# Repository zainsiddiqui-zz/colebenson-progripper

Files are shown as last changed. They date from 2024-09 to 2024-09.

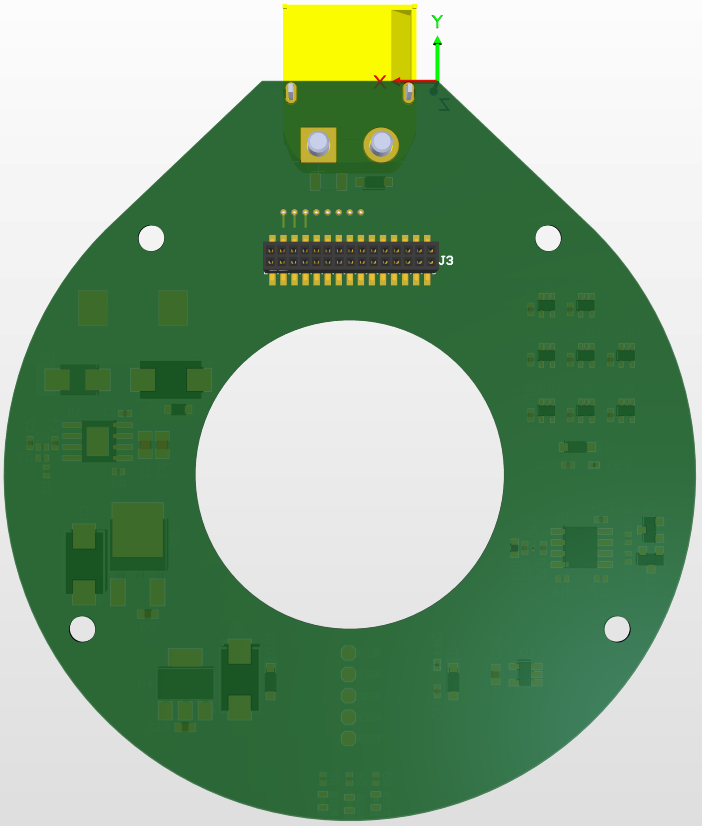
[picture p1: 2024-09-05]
Design Files/LSS_Gripper_Top_Board/Renderings/TopBoard-Bottomside.png

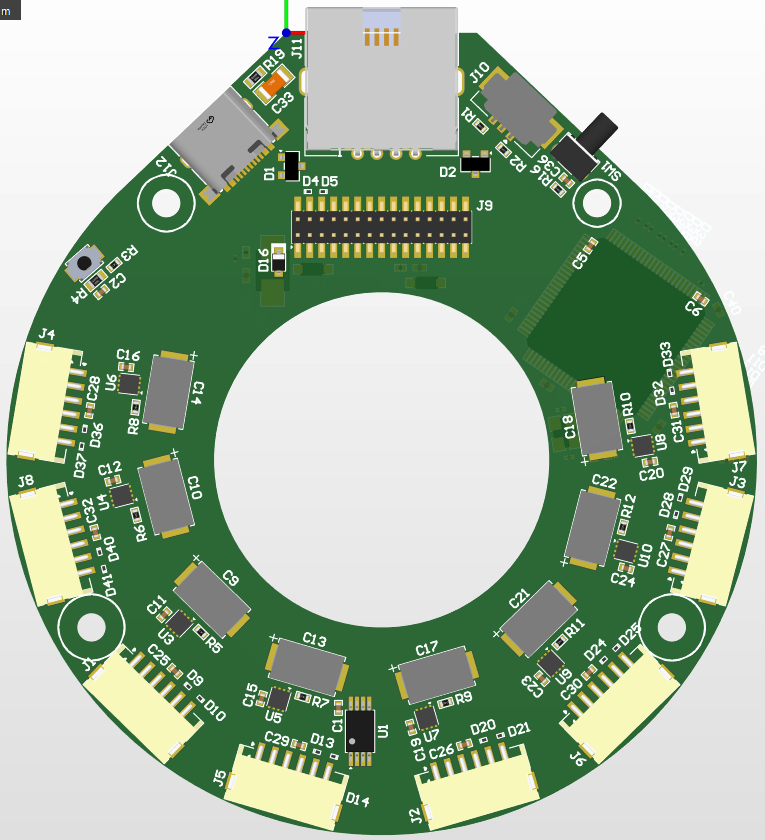
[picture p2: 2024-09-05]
Design Files/LSS_Gripper_Bottom_Board/Renderings/BottomBoard-Topside.png

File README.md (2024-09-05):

# LSS Modular Variable Gripper
### Client Name: Cole Benson (Robotshop)

## Requirements
The product should be compatible with LSS PRO Servos PCB design (electrical and communication). The idea behind the product is to be able to create robotic fingers for controlling and picking things. Each finger will have two motors to allow both parallel and angular motion. Some of the core features of the product are:
* Microcontroller: STM32F407 (same as LYN PRO Servos)
* CAN chip (same as LYN PRO servos)
* Voltage regulation (ex. 36 -> 12V for motors). The max input voltage will be 36V.
* DC Motor Controllers
    * Current detection (ideally stall detection and within motor controller but accessible to microcontroller)
* Connector on the DC Motor is [ZHR-6](https://github.com/eSpark-Consultants/colebenson-progripper/files/14555300/0900766b81357f31.pdf). Appropriate mating will be required on the PCB.
* XT60 Connector (~30 to 36V input, perhaps a bit more for max). These should be same as LSS PRO Servos. This should be on top board.
* RJ45 Connector (same pinout as PRO servos). This should be on bottom board.
* USB for reprogramming and firmware updates
* RGB LED at 90 degrees
* Button at 90 degrees
* Proposed Motor Driver chips
    * [DRV8214](https://www.ti.com/lit/ds/symlink/drv8214.pdf)
    * [DRV8234](https://www.ti.com/lit/ds/symlink/drv8234.pdf)
* When the traveler reaches either end of the lead screw, it will be physically stopped by the frame. The current will spike and it needs to automatically stop the motor. The microcontroller should not be needed for this.
* The microcontroller needs to read the current consumed by both motors in order to translate that to a force estimate acting on either motor. This should ideally be integrated into driver chip.
* Reading encoder position and/or the new method of ripple counting. The more that's done by the motor controller, the better. but traveler's absolute linear position will be required in the end (convert rotations to linear position)
* TI Article [Sensorless position and speed control](https://www.ti.com/lit/ab/slvafr5/slvafr5.pdf)
* The motor datasheet is pushed to docs folder. It also contains a more detailed PRD received from client!
* PCB mount temperature sensor on either top board or bottom board (depending on which board will have the MCU or most sensitive to heat circuitry). This sensor will be for measuring PCB temperature only.

## Nomenclature (Concept Image)


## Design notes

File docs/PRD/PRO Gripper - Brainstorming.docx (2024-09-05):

# Modular Variable Gripper Brainstorming

2024-02-06

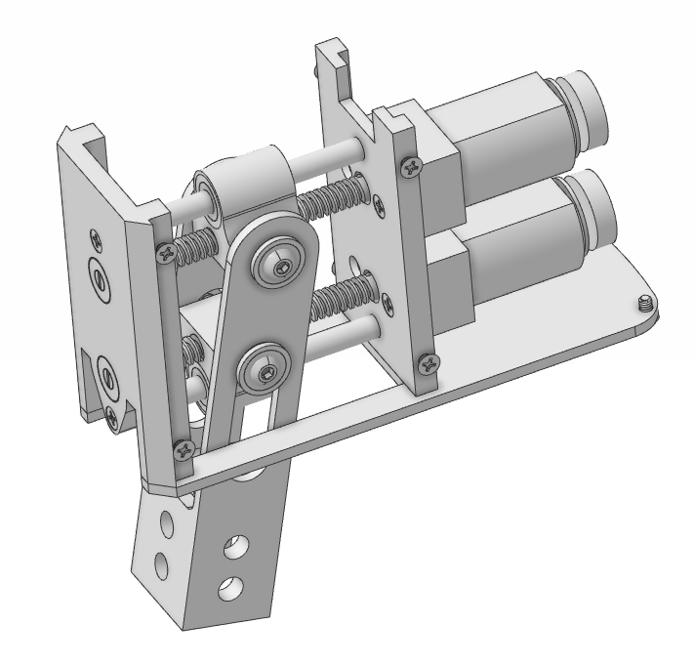
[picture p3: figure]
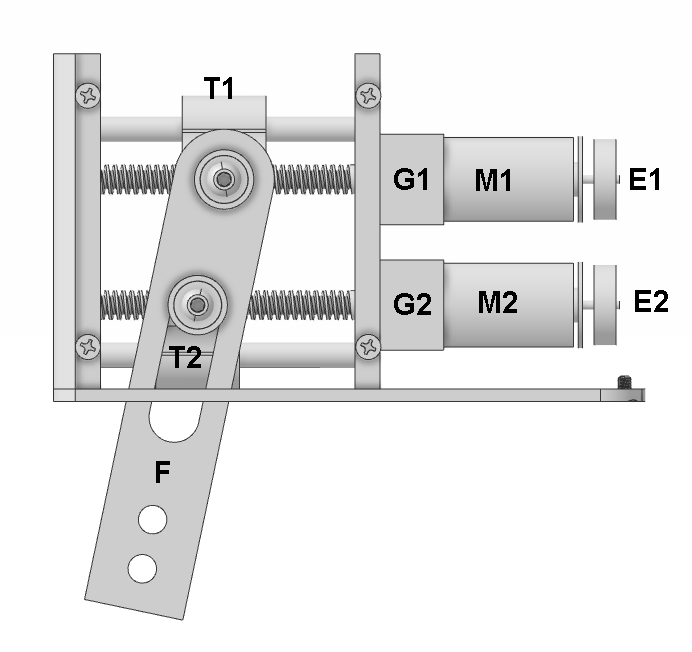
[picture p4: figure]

Frame removed to view internal components

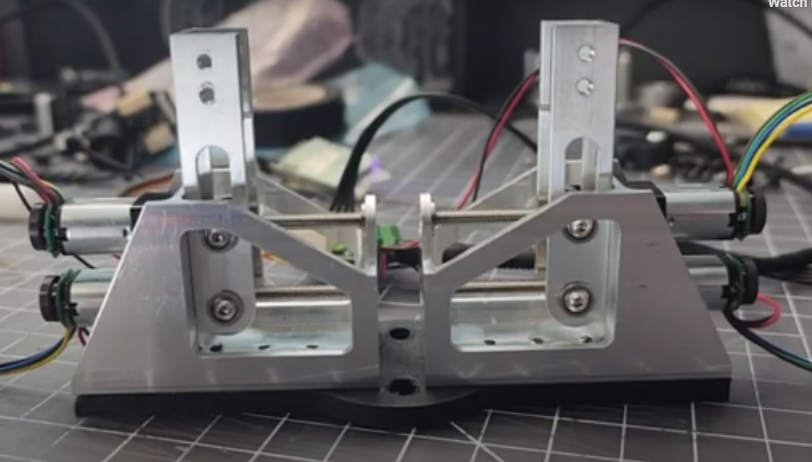
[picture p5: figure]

https://youtu.be/o8JT-9tQeA8

Side view of latest proof of concept prototype using 50:1 geared DC motor

# CONCEPT

The design has been in the works for a long time, and is finally to the point where the electronics and firmware can be brainstormed. The objective is to design and release a gripper with the following key features:

- Works with the Lynxmotion PRO arms without issue
  - Mechanically easy to integrate
  - Same input (electrical and communication connections) as PRO
  - Similar protocol to PRO Servos
  - Integrated into PRO arm software
- Acceptable overall specifications
  - Good opening for <1Kg objects and general applications / experimentation
  - Acceptable max force
  - Not as fast as a dedicated single motor parallel gripper (high speed application)
  - Lightweight
- Novel features
  - Two motors per finger allows parallel and angular motion
  - Configured as two or three fingers
  - Three mounting positions for larger opening
  - Very low MSRP compared to many grippers on the market

# RESPONSIBILITIES

Mechanics

- Coleman (lead)
- Eric N.

Electronics

- Huzaifa (lead)
- Hirokazu (verification)

Firmware

- Hirokazu
- Yves

Testing & Integration

- Yves (PRO Arm UI)
- Geraldine (ROS 2)
- Eduardo

# MECHANICS

2x Identical DC Gear Motors (M1, M2) Datasheet (https://drive.google.com/file/d/172SzxEvToy6MRe1LB5E0_673zfDenXMR/view?usp=drive_link)

- 12V nominal
- 5V encoder on motor’s rear shaft, 5 CPR (E1, E2)
- 50:1 Gear down (G1, G2)
- Tr3.5 Threaded shaft, ~34mm long

2x Identical Travelers (T1, T2)

- Tr3.5 threaded portion for motor’s shaft
- 3mm Linear bearing or bushing for stability
- Ball bearing for rotation for T1
- Ball bearing or Delrin for linear and rotational motion for T2

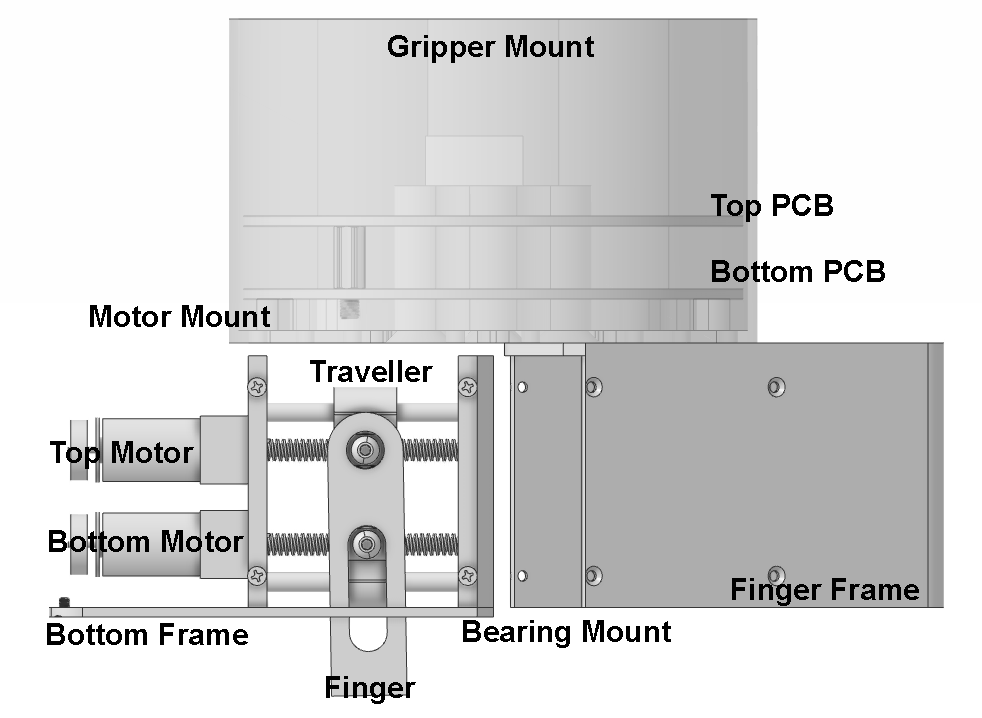
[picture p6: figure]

Nomenclature

# ELECTRONICS

The electronics can be mounted at the end of the last joint, between the end of the gearbox and inside the gripper mount so the fingers are not extended far beyond the last joint.

- Microcontroller: STM32F407 (same as LYN PRO Servos)
- CAN chip (same as LYN PRO servos)
- Voltage regulation (ex. 36 -> 12V for motors)
- DC Motor Controllers (Appendix)
  - Current detection (ideally stall detection and within motor controller but accessible to microcontroller)
- XT60 Connector (~30 to 36V input, perhaps a bit more/less for max)
- RJ45 Connector (same pinout as PRO servos)
- USB for reprogramming and firmware updates (perhaps hidden)
- RGB LED at 90 degrees (functionality TBD, much like the PRO servo)
- Button at 90 degrees (functionality TBD, much like the PRO servo)

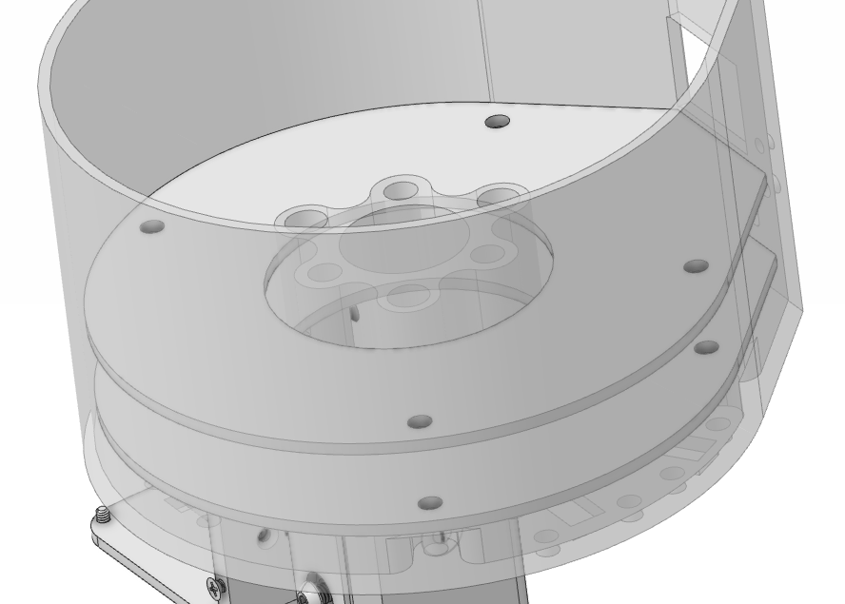
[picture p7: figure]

- Motor connections
  - Given there are five possible mounting points for a finger, with two motors to be connected via each opening, there can either be 10 total connectors or if the cable connecting the motor to the PCB is long enough , two openings can share the same two connectors, for 6 total.

PCB Stack

- Four M3 mounting holes
- 10mm (can be extended up to 12mm) standoffs separating PCBs
- 5mm distance between bottom PCB and
- We will provide a layout for each PCB denoting the max height for components on the top and bottom.
- Inexpensive male / female interconnect

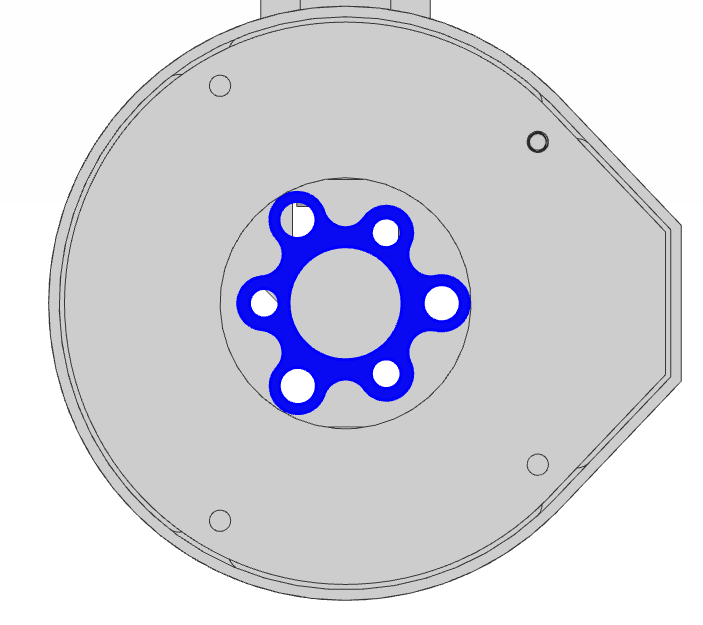
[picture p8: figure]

Center pattern using three screws for either LITE or STANDARD PRO servo.

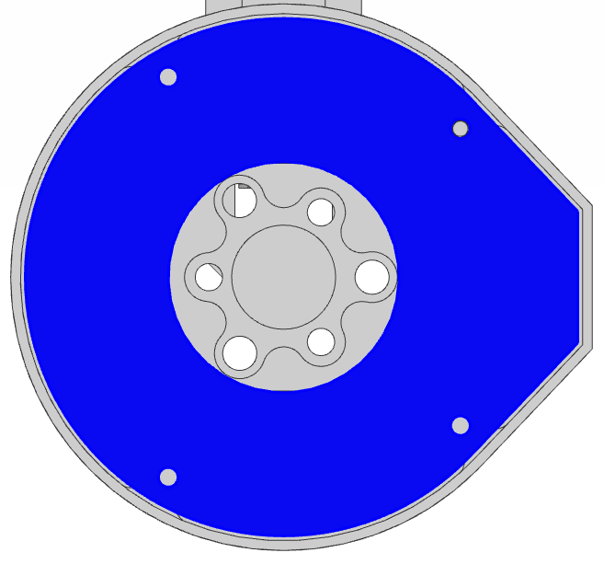
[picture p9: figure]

PCB shape

- Inner radius: 35.5mm (min) to 36mm
- Outer radius: 38mm to 39.75mm (max)
- Protrusion for RJ45 & XT60: TBD

FIRMWARE

- Gripper can be assigned an ID, or each finger assigned an ID
- Most of the basic LSS PRO Communication protocol reused, but new commands needed for linear position and angle
- Zeroing each finger based on stall detection, each time upon startup
  - Have M1 move at slow speed until it hits the mount then
  - Have M2 move at slow speed until it hits the mount
- Parallel motion accomplished by reading the encoder counts and ensuring they are the same by adjusting speed using PID (same concept as 2WD accurately maintaining a straight line)
- Angular motion accomplished by reading the encoder counts

SAFETY

- Once each motor has been zeroed, the firmware would consider the total linear travel possible vs. total encoder counts to ensure each motor does not go beyond the travel in either direction
- The force is limited, so it’s doubtful that anyone will be harmed if the fingers close on a human finger or something else.

# UNCERTAINTIES

- (CB) Working on a way to get smooth and accurate linear and rotational motion for T2 rather than direct bearing to metal contact.
- (EN) 50:1 DC gear motor seems to provide significantly more torque and higher travel speed compared to 50:1 geared stepper motor. However, the stepper’s motion is based on steps and unless one is skipped (detected in the controller), the motion of each motor should be identical. Is DC the best option?
- (CB) Finding the best DC motor controller with all the features we want.
- (CB) The design as such does not conform to any industry standards; from the mounting (specific to the LITE and STD servos), to the electronics and communication and the fingers / mounting pattern.

# QUESTIONS

1. (EN) How accurately do you think you can make the linear position for each motor to ensure the finger remains at a fixed angle?
  a. (ED) This would depend on the number of pulses of the encoder or the number of poles of the motor if we use the sensorless approach, it would also depend on the backlash between the mechanical parts.
    i. (CB) We have received a few prototypes from this company and there’s play in the output shaft of the gear motor (the threaded shaft), and it can move into and be pulled away from the motor by perhaps 0.25mm.
  b. (ED) Since we are using a 3.5mm pitch threaded shaft, it should move 3.5mm for each revolution, so in the case of the encoder we have 5 pulses for each revolution and a gearbox of 50:1, so for the threaded shaft to make a turn it would take 50 motor revolutions equivalent to 250 encoder pulses, so we would have a resolution of 3.5mm/250 pulses which would be 0.014mm/pulse.
    i. (CB) Exactly.
  c. (ED) Using the sensorless approach, which measures the motor ripple, each pulse would correspond to the number of motor poles, in general there is one ripple for each pair of poles (so we need to know the number of poles of the motor). Both the DVR8214 and the DVR8234 have a digital output RC_OUT with a stream of pulses corresponding to the current ripple of the motor, so as with the encoder, to control the position we can calculate the amount of pulses needed to reach the desired position.
    i. (CB) Having never used that type of technology, can it be trusted to not lose any “counts” I wonder, or is a rear shaft encoder the best option, or even a combination of both somehow?
2. (EN) How to ensure each finger is at the same linear position and angle if one motor encounters a force but not the others?
  a. (ED) To keep the same angle throughout the entire movement it is necessary that both motors move at the same speed, when one of the two detects an excess of current both motors of the same finger should be stopped. The force at T1 and T2 will be different in most cases so the driver must take this into account, the proposed drivers can control the speed with variable voltages and loads, however the DRV8214 is better than the DRV8234 because it is able to measure current with a higher resolution, the problem is that the output voltage is maximum 11V and the motors are 12V, so it would be best to use the DRV8234.
3. (CB) Given the current workload for the PRO (firmware and arm), how long would such firmware take to create?
4. (CB) Is there a way to use current detection either on the motor controller chip or separately to do force feedback?
  a. (GB) Yes, both options are available with the drivers linked on the appendix. Both drivers have a current sense output that would allow a microcontroller to detect motor stall or changes in load conditions.
  b. (GB) Both drivers you suggested have this feature, however the, DRV8214 has higher accuracy because it allows you to adjust the gain factor, for the DRV8234 the gain is set to 1500 uA/A.

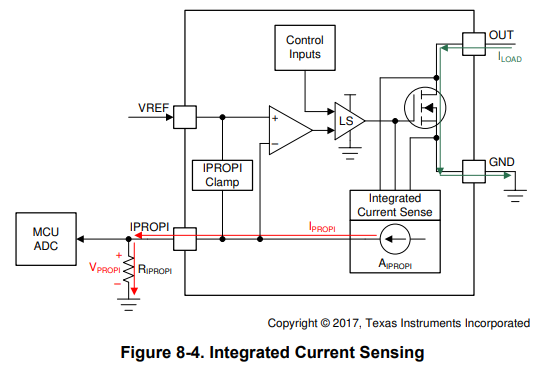
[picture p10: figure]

# The resistor on the IPROPI pin can provide a voltage signal to the microcontroller ADC. The RIPROPI resistor can be sized based on the expected load current in the application so that the full range of the controller ADC is utilized

Both drivers support hardware stall detection by comparing the IPROPI pin voltage to the VREF pin voltage, so using the VREF pin, the driver can regulate the motor current during startup and highload events without interaction from a microcontroller.

# APPENDIX

DC Gear Motor Datasheet

https://drive.google.com/file/d/172SzxEvToy6MRe1LB5E0_673zfDenXMR/view?usp=drive_link

New TI Chip (available July 2024):

https://www.ti.com/lit/ds/symlink/drv8214.pdf (only up to 11V)

https://www.ti.com/lit/ds/symlink/drv8234.pdf

Sensorless position and speed control:

https://www.ti.com/lit/ab/slvafr5/slvafr5.pdf

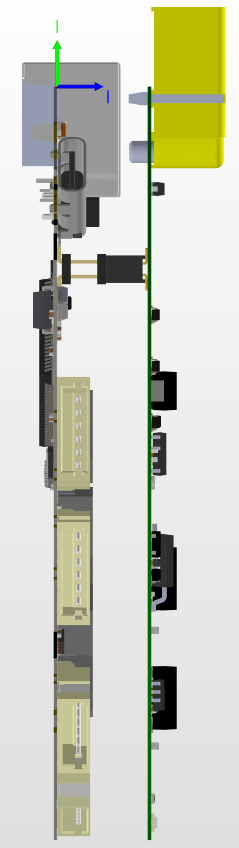
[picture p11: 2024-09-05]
Design Files/LSS_Gripper_Bottom_Board/Renderings/LeftSide-StackingUpTheBoards.png

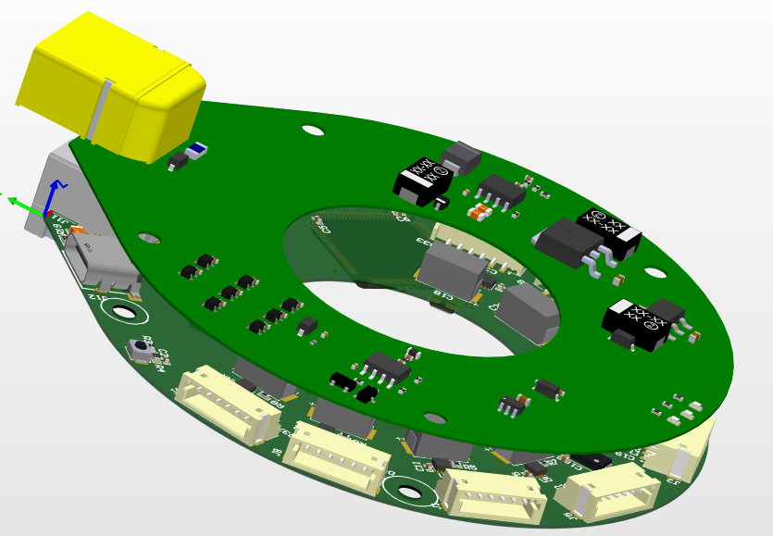
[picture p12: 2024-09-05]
Design Files/LSS_Gripper_Bottom_Board/Renderings/IsometricView01-StackingUpTheBoards.png

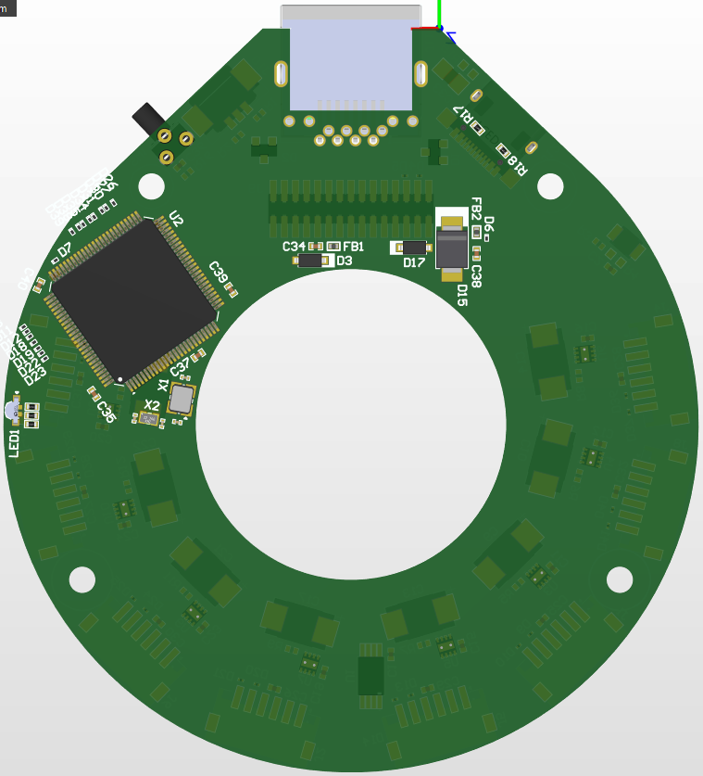
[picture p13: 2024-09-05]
Design Files/LSS_Gripper_Bottom_Board/Renderings/BottomBoard-Bottomside.png

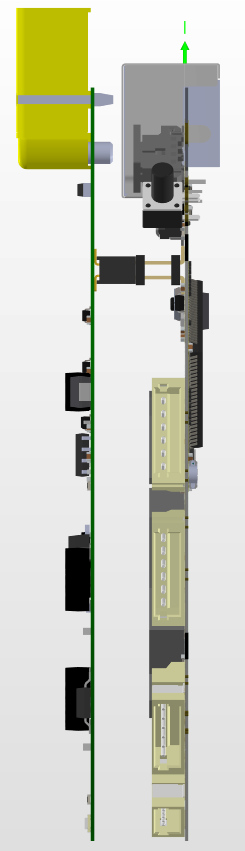
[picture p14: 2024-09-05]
Design Files/LSS_Gripper_Bottom_Board/Renderings/RightSide-StackingUpTheBoards.png

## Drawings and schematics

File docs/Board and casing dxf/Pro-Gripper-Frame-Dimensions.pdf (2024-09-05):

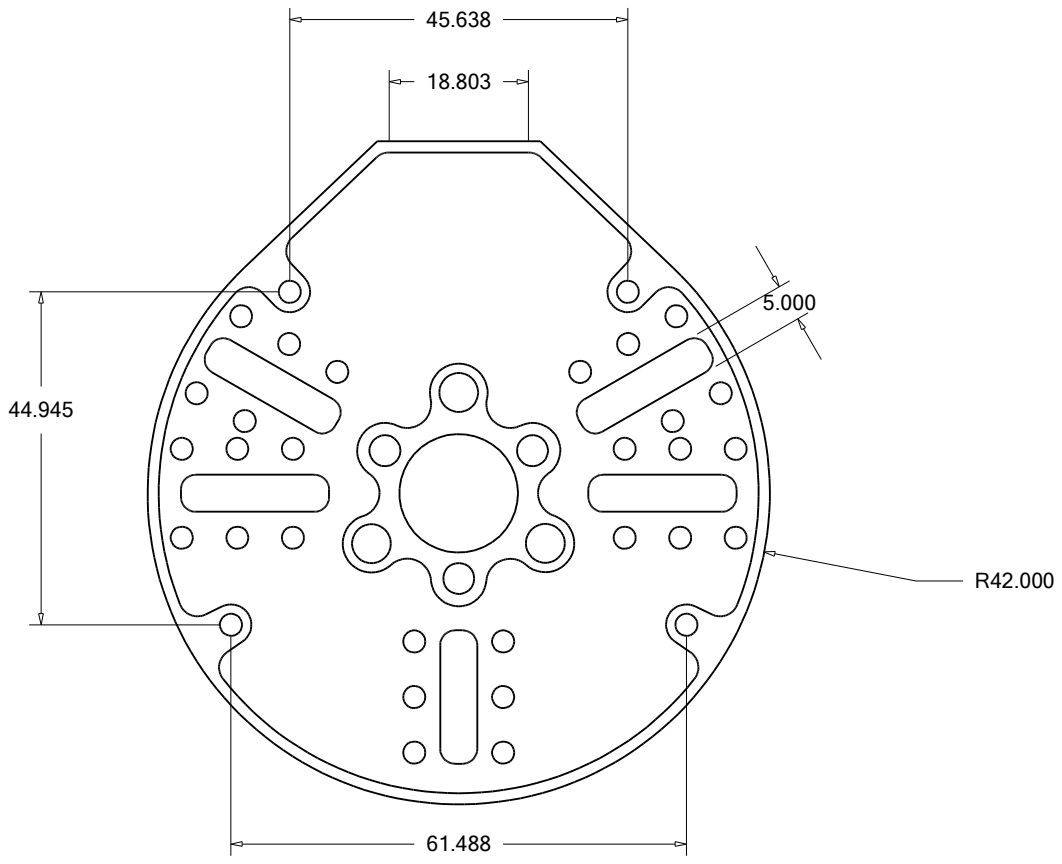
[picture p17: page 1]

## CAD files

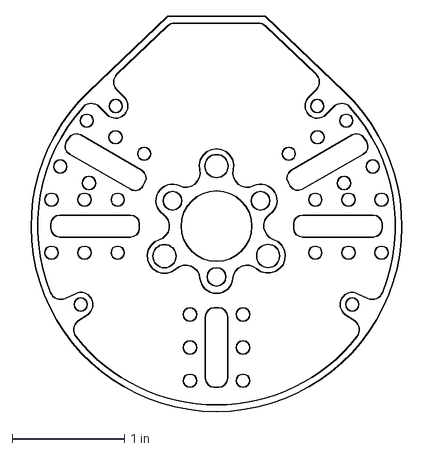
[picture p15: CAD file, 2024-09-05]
docs/Board and casing dxf/Pro-Gripper-Frame.dxf
3.57 x 3.52 in

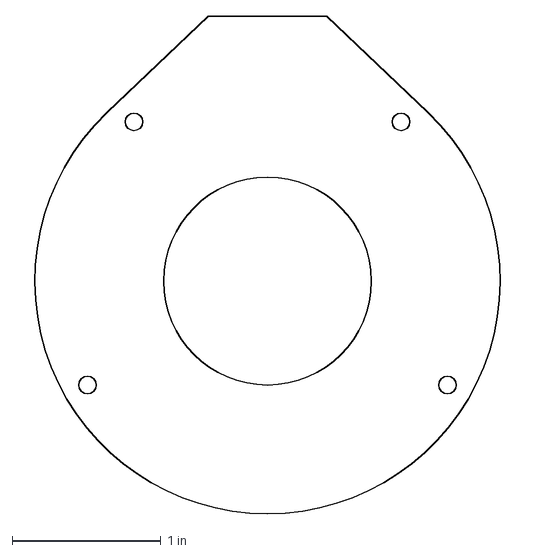
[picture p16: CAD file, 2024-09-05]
docs/Board and casing dxf/Gripper-PCB-v2.dxf
3.38 x 3.35 in
